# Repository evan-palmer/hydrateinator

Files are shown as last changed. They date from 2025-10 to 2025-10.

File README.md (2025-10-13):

# Hydrate-inator

https://github.com/user-attachments/assets/6a29c81f-0448-4756-8bf9-a8ebf71d8cc1

The Hydrate-inator is a drink serving robot that was used in my 
wedding. The project was put together by myself (Evan Palmer) and 
Charles Dawson, with help from Noel Palmer, Yanhao Yang, and Lydia 
Sylla. The Hydrate-inator successfully served over 150 guests (ages 
10-80 years old) ~15 gallons of water.

## Materials

The total cost of this project was roughly $238.88. The manufactured parts
were printed using a Prusa XL, and can be found in the `models/` directory.

| Name | Cost | Notes |
| ---- | ---- | ----- |
| Universal Robots UR10 | N/A | Borrowed from [Marble Technologies](https://www.seemarble.com/) |
| 3/8" Silicon Tubing (20') | $23.98 | [Amazon Link](https://www.amazon.com/dp/B089YGDB55) |
| 12V Power Supply | $20.99 | [Amazon Link](https://www.amazon.com/dp/B07MXXXBV8) |
| 1 GPM Diaphragm Pump | $28.99 | [Amazon Link](https://www.amazon.com/dp/B01N75ZIXF) |
| Pololu TB67H420FTG Motor Driver Carrier | $12.95 | [Pololu Link](https://www.pololu.com/product/2999) |
| Teensy 4.0 | $23.80 | [SparkFun Link](https://www.sparkfun.com/teensy-4-0.html) |
| Drip Tray | $46.39 | [Amazon Link](https://www.amazon.com/Kegco-KC-DP-125-Surface-Stainless/dp/B06WP5R2KD?sr=8-2) |
| Foldable Table | $44.98 | [Home Depot Link](https://www.homedepot.com/p/Lifetime-4-ft-One-Hand-Adjustable-Height-Fold-in-Half-Resin-Table-Almond-80943/322152748) |
| 5 Gallon Water Jug | $33.85 | [Amazon Link](https://www.amazon.com/Gallon-Plastic-Crown-Bottle-Container/dp/B01LZQFIFO?sr=8-3) |
| IR Break Beam Sensors | $2.95 | [Adafruit Link](https://www.adafruit.com/product/2167) |

## License

This project has been released under the MIT license.

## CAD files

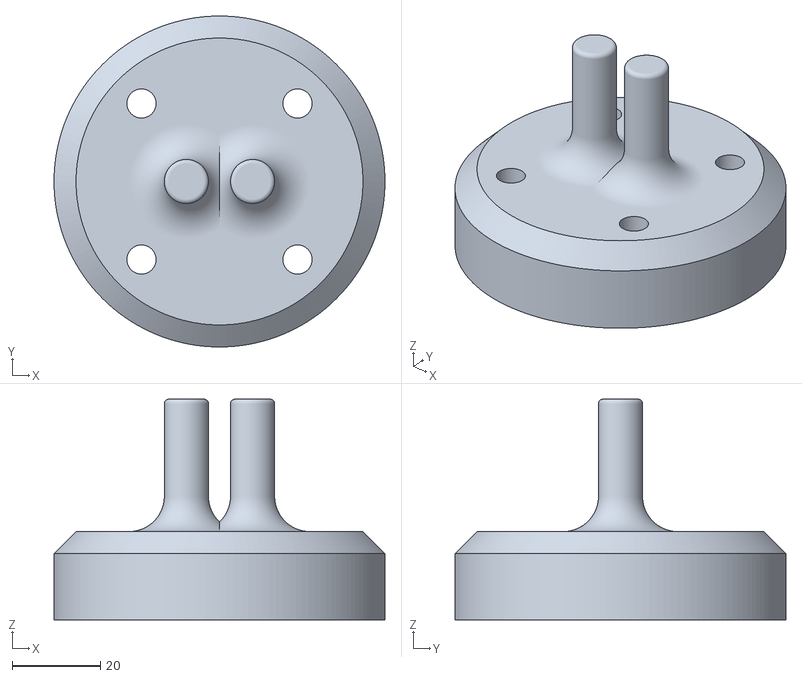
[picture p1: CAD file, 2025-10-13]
models/end_effector_attachment.stl
75.0 x 75.0 x 50.0

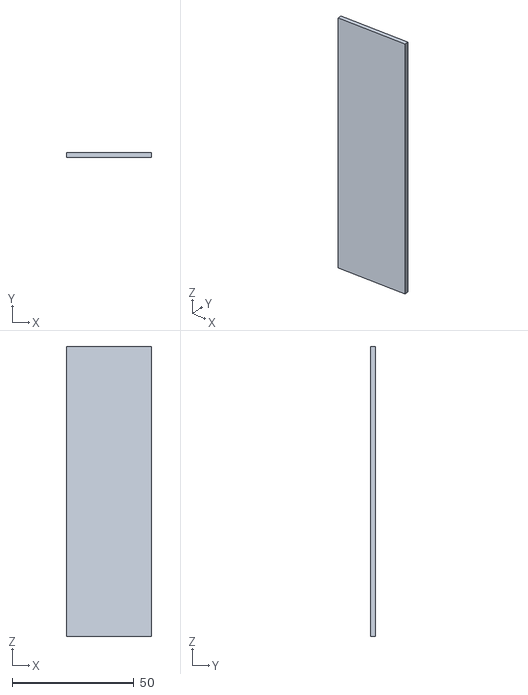
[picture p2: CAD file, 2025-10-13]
models/stand_cover.stl
35.0 x 2.00 x 119.0

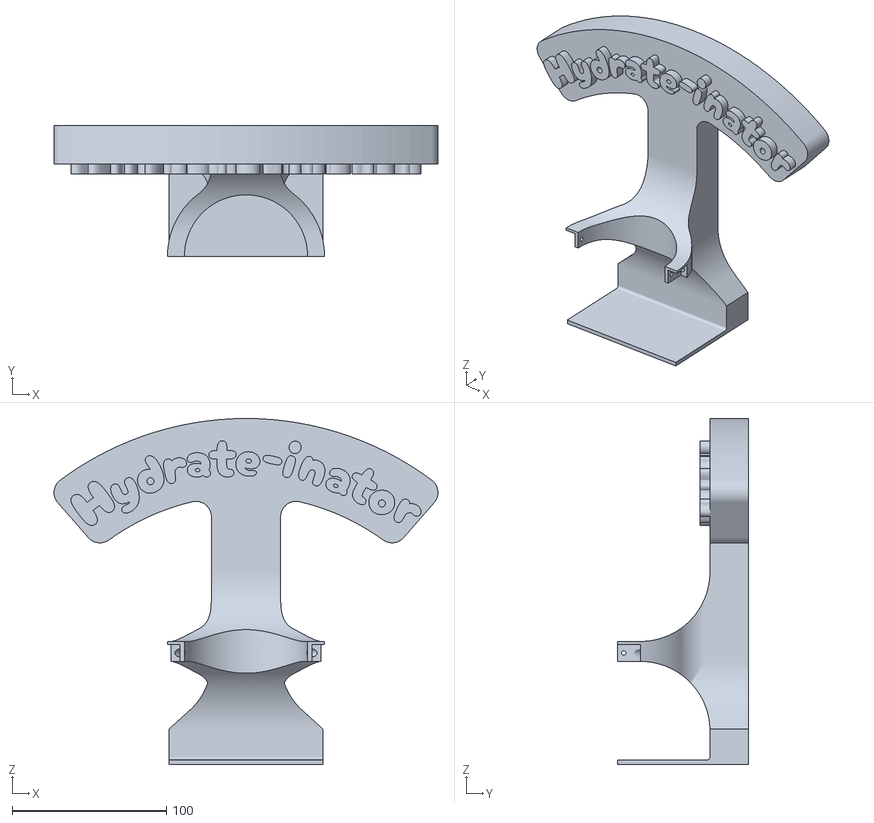
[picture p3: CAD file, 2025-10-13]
models/stand.stl
249.3 x 85.0 x 224.7

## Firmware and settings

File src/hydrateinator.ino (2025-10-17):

#include "hydrateinator.h"

void setup() {
  // configure the pump
  pinMode(PUMP_INA1_PIN, OUTPUT);
  pinMode(PUMP_INA2_PIN, OUTPUT);
  pinMode(PUMP_PWMA_PIN, OUTPUT);

  // configure the UR GPIO pins
  pinMode(UR_READY_PIN, INPUT);
  pinMode(UR_TO_HOLDER_PIN, OUTPUT);
  pinMode(UR_TO_STOW_PIN, OUTPUT);

  // configure the breakbeam sensor pins and set the internal pullup resistor
  pinMode(BREAKBEAM_PIN, INPUT);
  digitalWrite(BREAKBEAM_PIN, HIGH);
}

void loop() {
  if (is_cup_present()) {
    if (!is_manipulator_ready()) {
      move_to_fill_position();
    } else {
      unsigned long start_time = millis();
      run_pump();

      while (is_cup_present() && (millis() - start_time) < MAX_FILL_TIME_MS) {
        continue;
      }

      stop_pump();
      move_to_stow_position();
    }
  } else {
    stop_pump();
    move_to_stow_position();
  }

  delay(10);
}

int normalize_speed(float speed) {
  speed = constrain(speed, 0.0, 1.0);
  return (int)(speed * (PWM_MAX - PWM_MIN)) + PWM_MIN;
}

bool is_cup_present() {
  return !(bool)digitalRead(BREAKBEAM_PIN);
}

bool is_manipulator_ready() {
  return (bool)digitalRead(UR_READY_PIN);
}

void move_to_fill_position() {
  digitalWrite(UR_TO_STOW_PIN, LOW);
  digitalWrite(UR_TO_HOLDER_PIN, HIGH);
}

void move_to_stow_position() {
  digitalWrite(UR_TO_HOLDER_PIN, LOW);
  digitalWrite(UR_TO_STOW_PIN, HIGH);
}

void run_pump() {
  digitalWrite(PUMP_INA1_PIN, HIGH);
  digitalWrite(PUMP_INA2_PIN, LOW);
  analogWrite(PUMP_PWMA_PIN, normalize_speed(0.7));
}

void stop_pump() {
  digitalWrite(PUMP_INA1_PIN, LOW);
  digitalWrite(PUMP_INA2_PIN, LOW);
}

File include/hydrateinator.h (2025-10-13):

// breakbeam IR sensor pins
const uint8_t BREAKBEAM_PIN = 1;

// pump motor driver pins
const uint8_t PUMP_INA1_PIN = 2;
const uint8_t PUMP_INA2_PIN = 3;
const uint8_t PUMP_PWMA_PIN = 4;

// UR GPIO pins
const uint8_t UR_READY_PIN = 9;
const uint8_t UR_TO_HOLDER_PIN = 11;
const uint8_t UR_TO_STOW_PIN = 10;

// PWM configuration
const uint8_t PWM_MIN = 0;
const uint8_t PWM_MAX = 255;

// cup fill configuration
const unsigned long MAX_FILL_TIME_MS = 5000;  // 5s

/// Get the desired PWM value given a speed from 0.0 to 1.0.
int normalize_speed(float speed);

/// Check whether or not a cup is located in the cup holder.
bool is_cup_present();

/// Check whether or not the robot is in the fill position.
bool is_manipulator_ready();

/// Move the robot to the fill position.
void move_to_fill_position();

/// Move the robot to the stow position.
void move_to_stow_position();

/// Run the pump.
void run_pump();

/// Stop the pump.
void stop_pump();

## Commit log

2025-09-25 pump interface
2025-10-10 Update to use latest teensy code
2025-10-13 working on readme
    [end_effector_attachment.stl, stand.stl, stand_cover.stl]
2025-10-13 switch to gif
